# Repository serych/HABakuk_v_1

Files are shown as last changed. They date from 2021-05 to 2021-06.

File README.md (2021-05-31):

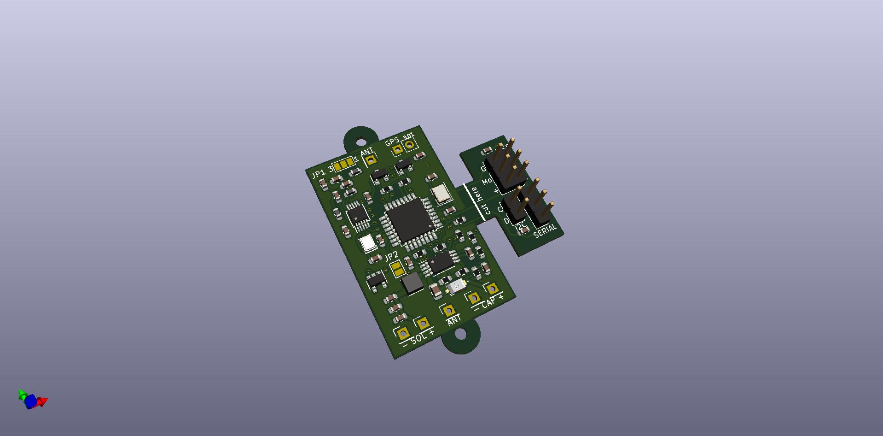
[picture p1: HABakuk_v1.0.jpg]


# HABakuk Pico Balloon Tracker Board

## Introduction:

Design of this board is based on excelent Alain's (K1FM) [K1FM-Pico-Balloon version 1.3](https://github.com/adecarolis).  Why I didn't use Alain's board directly and made my own PCB forked from his design? I was thinking about WSPR balloon tracker design for a long time (approximately 2-3 years) and I wanted simple board with ATmega328, Si5351 and Ublox GPS with possibility to switch peripheries off. From the board designs I found on the Internet, K1FM board met my original ideas the most but:  
- I wanted to power the board by solar panels via MPPT regulator (theorethicaly only two 50 x 25 mm panels would be enought to supply the board)
- I wanted the HF filter, but bypassable to test if the signal penetration is better with or without the filter 
- I'm designing my boards in KiCAD now, so I wanted to redraw the design completely (it is better than trying to import Eagle files) 

## Board construction:
The board includes MPPT power converter based on the SPV1040 chip and the values of the discrete components around it are calculated using [STMicroelectronics eDesignSuite](https://eds.st.com/photovoltaic/) using input parameters Voc = 1200 mV, Imp = 500 mA (measured on two solar panels in series) and Vmp = 930 mV, Imp = 450 mA (my estimation). There is connector for THT electrolytic capacitor serving as the energy store on the board. 

HF filter can be bypassed using **JP1** by scratching off solder jumper contact 1 (which is bridged on PCB by default) and soldering contact 3. 

I'm not sure if the measurement of solar panel voltage by the ATmega will not interfere with the SPV1040 power converter function, so I placed **JP2** on the board (bridged by default) which can be easily scratched off to break the (solar panel -> AD converter input) connection in the case of any problems.
                                                                                                          
The board is designed as 4 layers (only 3 layers used) thin PCB (it has thicknes of 0.8 mm only to reduce the weight of the PCB). Also there is filled zone (GND) only on one side of the board to reduce the weight. All the components except the Ublox GPS module are placed on the top side of the board to make the reflow soldering possible in the amateur conditions.  GPS module on the back side of the board should be soldered as the last component by the soldering iron.      

## Software: 
The recommended softwares are [OrionWSPR](https://github.com/ve3wmb/OrionWspr) or [GeminiWSPR](https://github.com/adecarolis/GeminiWspr)

## Production and real tests
The board will be ordered in [LJCPCB](https://jlcpcb.com/) and I will add here the link to reorder it.

**The board was not yet produced nor tested!** 

Jakub Šerých, serych@panska.cz, [https://jakub.serych.cz](https://jakub.serych.cz) (web only in Czech language)

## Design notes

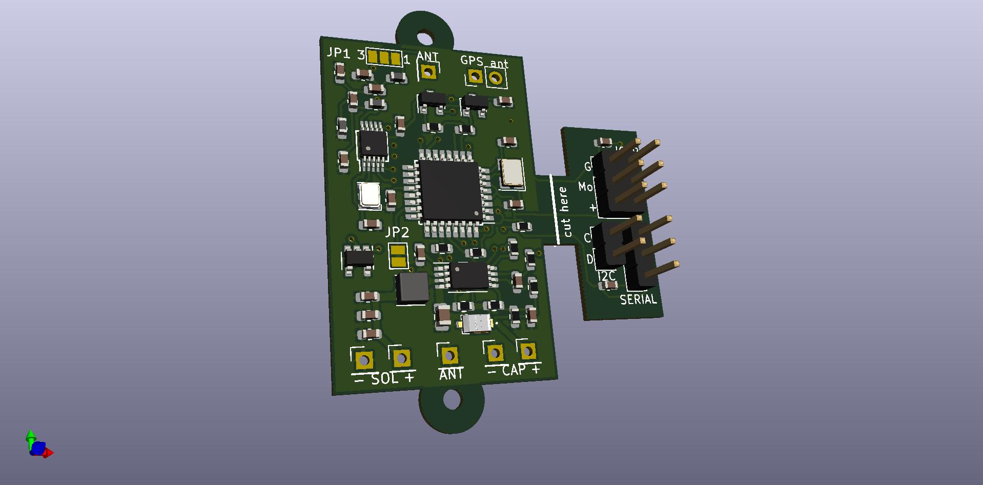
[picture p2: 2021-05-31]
3D views/front.jpg

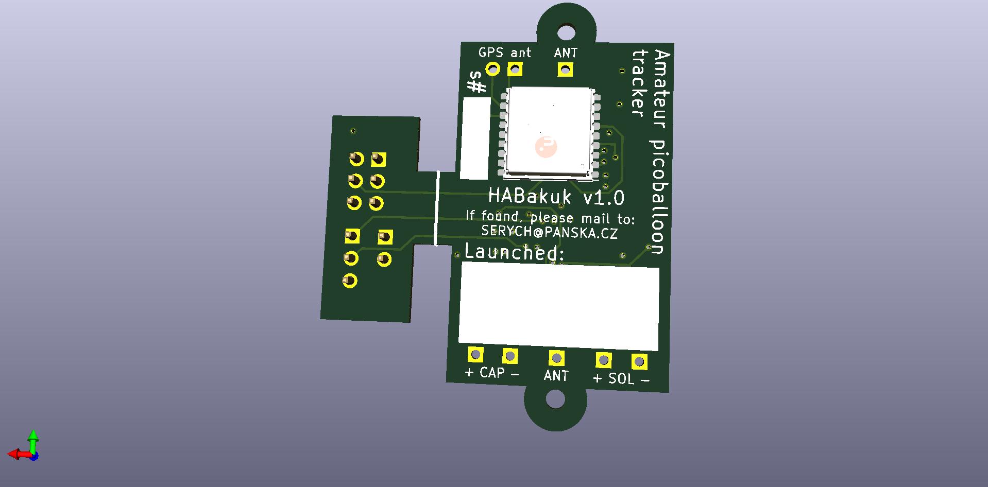
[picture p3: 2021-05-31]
3D views/back.jpg

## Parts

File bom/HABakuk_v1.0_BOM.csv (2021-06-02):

Id | Designator | Package | Quantity | Designation | Supplier and ref
1 | D1 | STMITE | 1 | SMM4F5.0A-TR
2 | J10 | PinHeader_1x01_P2.54mm_Vertical | 1 | C-
3 | J9 | PinHeader_1x01_P2.54mm_Vertical | 1 | C+
4 | J8 | PinHeader_1x01_P2.54mm_Vertical | 1 | SOL-
5 | J7 | PinHeader_1x01_P2.54mm_Vertical | 1 | SOL+
6 | J6 | PinHeader_1x01_P2.54mm_Vertical | 1 | ANT_DWN
7 | J5 | PinHeader_1x01_P2.54mm_Vertical | 1 | ANT_UP
8 | J4 | PinHeader_1x02_P2.54mm_Vertical | 1 | GPS_Ant
9 | J3 | PinHeader_1x03_P2.54mm_Vertical | 1 | SERIAL
10 | J2 | PinHeader_1x02_P2.54mm_Vertical | 1 | I2C
11 | JP2 | SolderJumper-2_P1.3mm_Bridged_Pad1.0x1.5mm | 1 | SolderJumper_2_Bridged
12 | REF**,REF** | MountingHole_2.1mm | 2 | MountingHole_2.1mm
13 | Y1 | Crystal_SMD_Abracon_ABM8G-4Pin_3.2x2.5mm | 1 | Crystal_GND24_Small
14 | U6 | SOT-23-5 | 1 | TMP36GRT
15 | U5 | Oscillator_SMD_Kyocera_2520-6Pin_2.5x2.0mm | 1 | 25MHz
16 | U4 | ublox_MAX | 1 | MAX-M8Q
17 | U3 | MSOP-10_3x3mm_P0.5mm | 1 | Si5351A-B-GT
18 | U2 | TQFP-32_7x7mm_P0.8mm | 1 | ATmega328P-AU
19 | U1 | TSSOP-8_4.4x3mm_P0.65mm | 1 | SPV1040T
20 | R11,R7,R3,R2,R1 | R_0603_1608Metric | 5 | 1k
21 | R10,R9 | R_0603_1608Metric | 2 | 4k7
22 | R8 | R_0603_1608Metric | 1 | 10k
23 | R6 | R_0603_1608Metric | 1 | 220k
24 | R5 | R_0603_1608Metric | 1 | 360k
25 | R4 | R_0603_1608Metric | 1 | 510m
26 | Q2,Q1 | SOT-23 | 2 | SSM3J135TU
27 | L4,L3,L2 | L_0603_1608Metric | 3 | 1,5u
28 | L1 | L_Taiyo-Yuden_MD-3030 | 1 | 10u
29 | JP1 | SolderJumper-3_P1.3mm_Bridged12_Pad1.0x1.5mm_NumberLabels | 1 | fltr
30 | J1 | PinHeader_2x03_P2.54mm_Vertical | 1 | ICSP
31 | C21,C5 | C_0603_1608Metric | 2 | 1u
32 | C20,C16 | C_0603_1608Metric | 2 | 56p
33 | C19,C17 | C_0603_1608Metric | 2 | 18p
34 | C18 | C_0603_1608Metric | 1 | 47p
35 | C15,C10,C8 | C_0603_1608Metric | 3 | 0,1u
36 | C14,C9 | C_0603_1608Metric | 2 | 0,47u
37 | C12,C11 | C_0603_1608Metric | 2 | 15p
38 | C7 | C_0805_2012Metric | 1 | 10u/10
39 | C6,C4 | C_0603_1608Metric | 2 | 1n
40 | C3,C2,C1 | C_0603_1608Metric | 3 | 10u/4

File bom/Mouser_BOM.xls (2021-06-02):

NÁKUPNÍ VOZÍK
Toto není faktura
02-čvn-21 16:34:00
 | Č. Mouser | Výr. Č. | Výrobce | číslo zákazníka | Popis | RoHS: | Životní cyklus | Objednaný počet | Cena (CZK) | Ext.: (CZK)
1 | 377-MAX-8Q-0 | MAX-8Q-0 | u-blox | 16 | Moduly GPS u-blox 8 GNSS LCC module, TCXO, ROM: Due to supply constraint, recommend PN - MAX-8C-0 |  | Mouser nově nabízí | 1 | 488,11 Kč | 488,11 Kč
2 | 511-SPV1040T | SPV1040T | STMicroelectronics | 19 | Řízení baterie Hi efficiency solar battery charger | V souladu RoHS |  | 1 | 74,41 Kč | 74,41 Kč
3 | 511-SMM4F5.0A-TR | SMM4F5.0A-TR | STMicroelectronics | 1 | Ochrana před elektrostatickými výboji / Diody pro potlačení napětí z přechodových jevů 400W HI JCT TMP | V souladu RoHS |  | 1 | 13,10 Kč | 13,10 Kč
4 | 81-GRM188C80G106KE7D | GRM188C80G106KE47D | Murata | 40 | Vícevrstvé keramické kondenzátory MLCC – pro povrchovou montáž SMD, SMT 0603 10uF 4volts *Derate Voltage/Temp | V souladu RoHS |  | 3 | 4,43 Kč | 13,29 Kč
5 | 963-LMK212BJ106KD-T | LMK212BJ106KD-T | Taiyo Yuden | 38 | Vícevrstvé keramické kondenzátory MLCC – pro povrchovou montáž SMD, SMT 0805 10VDC 10uF 10% X5R | V souladu RoHS |  | 1 | 6,45 Kč | 6,45 Kč
6 | 673-PA4334103NLT | PA4334.103NLT | Pulse | 28 | Pevné cívky IND, PWR, 3X3X1.2 10 uH, SMT | V souladu RoHS |  | 1 | 9,54 Kč | 9,54 Kč
7 | 647-UMA0G471MDD | UMA0G471MDD | Nichicon | 50 | Hliníkové elektrolytické kondenzátory – s radiálním vývodem 4volts 470uF 8x5 20% 2.5LS | V souladu RoHS |  | 1 | 9,54 Kč | 9,54 Kč
8 | 652-CRL0603FWR510ELF | CRL0603-FW-R510ELF | Bourns | 25 | Rezistory ke snímání proudu - SMD 0.51ohm 1% 1/10watt | V souladu se směrnicí RoHS na základě výjimky |  | 1 | 4,43 Kč | 4,43 Kč
9 | 667-ERJ-3RED3603V | ERJ-3RED3603V | Panasonic | 24 | Tlustovrstvé rezistory – SMD 0603 Resistor 0.5% 100ppm 360KOhm |  |  | 1 | 2,44 Kč | 2,44 Kč
10 | 71-RCS0603220KFKEA | RCS0603220KFKEA | Vishay | 23 | Tlustovrstvé rezistory – SMD 0.25watt 220Kohms 1% 100ppm | V souladu se směrnicí RoHS na základě výjimky |  | 1 | 3,56 Kč | 3,56 Kč
11 | 755-SDR03EZPF1001 | SDR03EZPF1001 | ROHM Semiconductor | 20 | Tlustovrstvé rezistory – SMD 0603 1Kohm 1% Anti Surge AEC-Q200 | V souladu RoHS |  | 5 | 3,12 Kč | 15,60 Kč
12 | 187-CL03B102KO3NNNC | CL03B102KO3NNNC | Samsung Electro-Mechanics | 39 | Vícevrstvé keramické kondenzátory MLCC – pro povrchovou montáž SMD, SMT 1nF+/-10% 16V X7R 0603 | V souladu RoHS | Mouser nově nabízí | 2 | 2,88 Kč | 5,76 Kč
13 | 187-CL03A105KQ3CSNH | CL03A105KQ3CSNH | Samsung Electro-Mechanics | 31 | Vícevrstvé keramické kondenzátory MLCC – pro povrchovou montáž SMD, SMT 1uF+/-10% 6.3V X5R 0603 | V souladu RoHS | Mouser nově nabízí | 2 | 3,77 Kč | 7,54 Kč
14 | 757-SSM3J135TULF | SSM3J135TU,LF | Toshiba | 26 | MOSFET Small Signal MOSFET P-ch VDSS=-20V, VGSS=+/-8V, ID=-3.0A, RDS(ON)=0.103Ohm @ 4.5V, in UFM package | V souladu RoHS | Nový produkt | 2 | 8,44 Kč | 16,88 Kč
15 | 732-TG252S25MCGNNM3 | TG2520SMN 25.000M-MCGNNM3 | Epson | 15 | TCXO oscilátory TG2520SMN 25.000M-MCGNNM3: TCXO 2.8V 3.3V +/-0.5PPM -40 85C NON O/E250TR | V souladu RoHS | Nový produkt | 1 | 39,56 Kč | 39,56 Kč
16 | 634-SI5351A-B-GTR | SI5351A-B-GTR | Silicon Laboratories | 17 | Generátory hodin a podpůrné produkty I2C Prog, Any Frequency, Any Output, Xtal Ref, 3-Output LVCMOS Clock Gen | V souladu RoHS |  | 1 | 21,54 Kč | 21,54 Kč
17 | 584-TMP36GRTZ-R7 | TMP36GRTZ-REEL7 | Analog Devices Inc. | 14 | Snímače teploty montované na desku -3V TEMPERATURE SENSOR | V souladu RoHS |  | 1 | 42,71 Kč | 42,71 Kč
18 | 810-MLZ1608A1R5WT000 | MLZ1608A1R5WT000 | TDK | 27 | Pevné cívky 0603 1.5uH 20% Large Current | V souladu RoHS | Mouser nově nabízí | 3 | 3,33 Kč | 9,99 Kč
19 | 755-SDR03EZPJ472 | SDR03EZPJ472 | ROHM Semiconductor | 21 | Tlustovrstvé rezistory – SMD 0603 4.7Kohm 5% Anti Surge AEC-Q200 | V souladu RoHS |  | 2 | 2,23 Kč | 4,46 Kč
20 | 80-C0603C150K5RACTU | C0603C150K5RAC7867 | KEMET | 37 | Vícevrstvé keramické kondenzátory MLCC – pro povrchovou montáž SMD, SMT 50V 15pF X7R 0603 10% | V souladu RoHS |  | 2 | 5,32 Kč | 10,64 Kč
21 | 80-C0603C180K5RACTU | C0603C180K5RACTU | KEMET | 33 | Vícevrstvé keramické kondenzátory MLCC – pro povrchovou montáž SMD, SMT 50V 18pF X7R 0603 10% | V souladu RoHS |  | 2 | 5,32 Kč | 10,64 Kč
22 | 581-0603YC470KAT2A | 0603YC470KAT2A | AVX | 34 | Vícevrstvé keramické kondenzátory MLCC – pro povrchovou montáž SMD, SMT 16V 47pF X7R 0603 10% | V souladu RoHS | Nový produkt | 1 | 5,32 Kč | 5,32 Kč
23 | 77-VJ0603D560JXCAJ | VJ0603D560JXCAJ | Vishay | 32 | Vícevrstvé keramické kondenzátory MLCC – pro povrchovou montáž SMD, SMT 0603 56pF 200V C0G 5% HI FREQ | V souladu RoHS |  | 2 | 5,32 Kč | 10,64 Kč
24 | 80-C0603C104K3NAUTO | C0603C104K3NACAUTO | KEMET | 35 | Vícevrstvé keramické kondenzátory MLCC – pro povrchovou montáž SMD, SMT 25V 0.1uF X8L 0603 10% AEC-Q200 | V souladu RoHS |  | 3 | 3,77 Kč | 11,31 Kč
25 | 187-CL10A474KA8NNNC | CL10A474KA8NNNC | Samsung Electro-Mechanics | 36 | Vícevrstvé keramické kondenzátory MLCC – pro povrchovou montáž SMD, SMT 470nF+/-10% 25V X5R 1608 | V souladu RoHS | Mouser nově nabízí | 2 | 2,44 Kč | 4,88 Kč
26 | 71-CRCW060310K0JNEBC | CRCW060310K0JNEBC | Vishay | 22 | Tlustovrstvé rezistory – SMD 1/10Watt 10Kohms 5% Commercial Use | V souladu se směrnicí RoHS na základě výjimky |  | 1 | 2,23 Kč | 2,23 Kč
27 | 710-830055663 | 830055663 | Wurth Elektronik | 13 | Krystaly WE-XTAL 8.0MHz 30ppm 5.0 x 3.2mm | V souladu RoHS | Nový produkt | 1 | 16,87 Kč | 16,87 Kč
Předložením objednávky souhlasítes těmito lhuty a podmínky. (https://cz.mouser.com/saleterms) |  |  |  |  |  |  |  |  | Zboží: | 861,44 Kč
Ceny platí k uvedenému datu a času. |  |  |  |  |  |  |  |  | Přepravné: | 500,00 Kč
 |  |  |  |  |  |  |  |  | Odesílání položek, které nebyly na skladě: | 0,00 Kč

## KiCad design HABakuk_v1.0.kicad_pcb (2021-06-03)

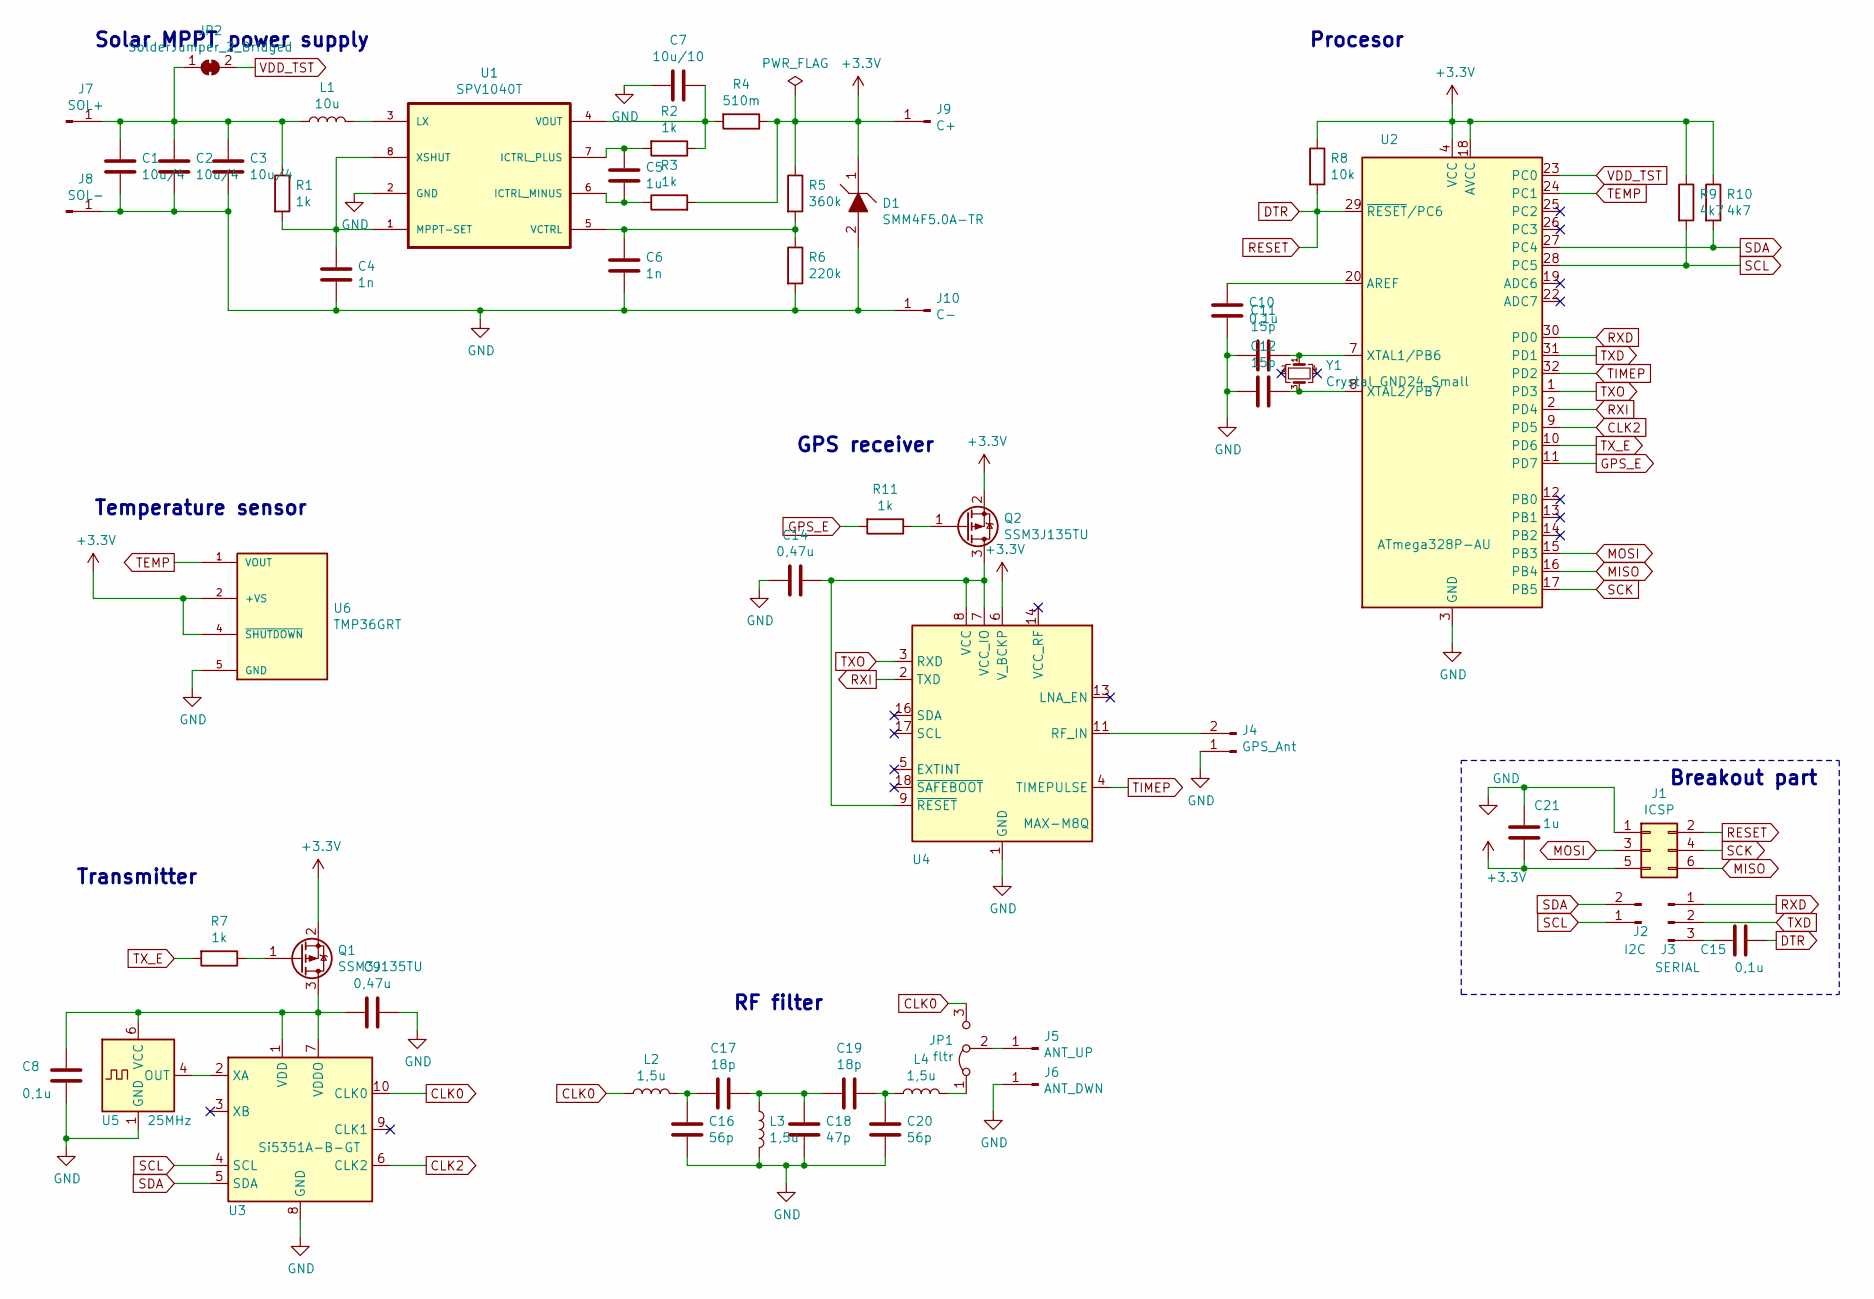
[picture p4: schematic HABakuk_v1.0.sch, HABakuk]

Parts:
C1, C2, C3: 10u/4; C_0603_1608Metric
C4, C6: 1n; C_0603_1608Metric
C5, C21: 1u; C_0603_1608Metric
C7: 10u/10; C_0805_2012Metric
C8, C10, C15: 0,1u; C_0603_1608Metric
C9, C14: 0,47u; C_0603_1608Metric
C11, C12: 15p; C_0603_1608Metric
C16, C20: 56p; C_0603_1608Metric
C17, C19: 18p; C_0603_1608Metric
C18: 47p; C_0603_1608Metric
D1: SMM4F5.0A-TR; STMITE; Mouser Part Number 511-SMM4F5.0A-TR
J1: ICSP; PinHeader_2x03_P2.54mm_Vertical
J2: I2C; PinHeader_1x02_P2.54mm_Vertical
J3: SERIAL; PinHeader_1x03_P2.54mm_Vertical
J4: GPS_Ant; PinHeader_1x02_P2.54mm_Vertical
J5: ANT_UP; PinHeader_1x01_P2.54mm_Vertical
J6: ANT_DWN; PinHeader_1x01_P2.54mm_Vertical
J7: SOL+; PinHeader_1x01_P2.54mm_Vertical
J8: SOL-; PinHeader_1x01_P2.54mm_Vertical
J9: C+; PinHeader_1x01_P2.54mm_Vertical
J10: C-; PinHeader_1x01_P2.54mm_Vertical
JP1: fltr; SolderJumper-3_P1.3mm_Bridged12_Pad1.0x1.5mm_NumberLabels
JP2: SolderJumper_2_Bridged; SolderJumper-2_P1.3mm_Bridged_Pad1.0x1.5mm
L1: 10u; L_Taiyo-Yuden_MD-3030
L2, L3, L4: 1,5u; L_0603_1608Metric
Q1, Q2: SSM3J135TU; SOT-23
R1, R2, R3, R7, R11: 1k; R_0603_1608Metric
R4: 510m; R_0603_1608Metric
R5: 360k; R_0603_1608Metric
R6: 220k; R_0603_1608Metric
R8: 10k; R_0603_1608Metric
R9, R10: 4k7; R_0603_1608Metric
U1: SPV1040T; TSSOP-8_4.4x3mm_P0.65mm
U2: ATmega328P-AU; TQFP-32_7x7mm_P0.8mm
U3: Si5351A-B-GT; MSOP-10_3x3mm_P0.5mm
U4: MAX-M8Q; ublox_MAX
U5: 25MHz; Oscillator_SMD_Kyocera_2520-6Pin_2.5x2.0mm
U6: TMP36GRT; SOT-23-5; PARTREV H
Y1: Crystal_GND24_Small; Crystal_SMD_5032-4Pin_5.0x3.2mm

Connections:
+3V3: C21.2, D1.1, J1.5, J9.1, Q1.2 (S), Q2.2 (S), R3.2, R4.1, R5.1, R8.1, R9.1, R10.1, U2.4 (VCC), U2.6 (VCC), U2.18 (AVCC), U4.6 (V_BCKP), U6.2 (+VS), U6.4 (~SHUTDOWN)
CLK0: JP1.3 (B), L2.1, U3.10 (CLK0)
CLK2: U2.9 (PD5), U3.6 (CLK2)
DTR: C15.1, J1.2, R8.2, U2.29 (~RESET~/PC6)
GND: C1.2, C2.2, C3.2, C4.2, C6.2, C7.2, C8.2, C9.1, C10.2, C11.2, C12.2, C14.2, C16.2, C18.2, C20.2, C21.1, D1.2, J1.1, J4.1, J6.1, J8.1, J10.1, L3.2, R6.2, U1.2 (GND), U2.3 (GND), U2.5 (GND), U2.21 (GND), U3.8 (GND), U4.1 (GND), U4.10 (GND), U4.12 (GND), U5.1 (GND), U5.3 (GND), U6.5 (GND)
GPS_E: R11.2, U2.11 (PD7)
MISO: J1.6, U2.16 (PB4)
MOSI: J1.3, U2.15 (PB3)
unnamed: C1.1, C2.1, C3.1, J7.1, JP2.1 (A), L1.1, R1.1
unnamed: C4.1, R1.2, U1.1 (MPPT-SET), U1.8 (XSHUT)
unnamed: C5.1, R2.2, U1.7 (ICTRL_PLUS)
unnamed: C5.2, R3.1, U1.6 (ICTRL_MINUS)
unnamed: C6.1, R5.2, R6.1, U1.5 (VCTRL)
unnamed: C7.1, R2.1, R4.2, U1.4 (VOUT)
unnamed: C8.1, C9.2, Q1.3 (D), U3.1 (VDD), U3.7 (VDDO), U5.6 (VCC)
unnamed: C10.1, U2.20 (AREF)
unnamed: C11.1, U2.7 (XTAL1/PB6), Y1.1
unnamed: C12.1, U2.8 (XTAL2/PB7), Y1.3
unnamed: C14.1, Q2.3 (D), U4.7 (VCC_IO), U4.8 (VCC), U4.9 (~RESET)
unnamed: C15.2, J3.3
unnamed: C16.1, C17.2, L2.2
unnamed: C17.1, C18.1, C19.2, L3.1
unnamed: C19.1, C20.1, L4.1
unnamed: J4.2, U4.11 (RF_IN)
unnamed: J5.1, JP1.2 (C)
unnamed: JP1.1 (A), L4.2
unnamed: L1.2, U1.3 (LX)
unnamed: Q1.1 (G), R7.1
unnamed: Q2.1 (G), R11.1
unnamed: U3.2 (XA), U5.4 (OUT)
RXD: J3.1, U2.30 (PD0)
RXI: U2.2 (PD4), U4.2 (TXD)
SCK: J1.4, U2.17 (PB5)
SCL: J2.1, R9.2, U2.28 (PC5), U3.4 (SCL)
SDA: J2.2, R10.2, U2.27 (PC4), U3.5 (SDA)
TEMP: U2.24 (PC1), U6.1 (VOUT)
TIMEP: U2.32 (PD2), U4.4 (TIMEPULSE)
TXD: J3.2, U2.31 (PD1)
TXO: U2.1 (PD3), U4.3 (RXD)
TX_E: R7.2, U2.10 (PD6)
VDD_TST: JP2.2 (B), U2.23 (PC0)

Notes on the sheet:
Breakout part
Transmitter
RF filter
Temperature sensor
GPS receiver
Solar MPPT power supply
Procesor

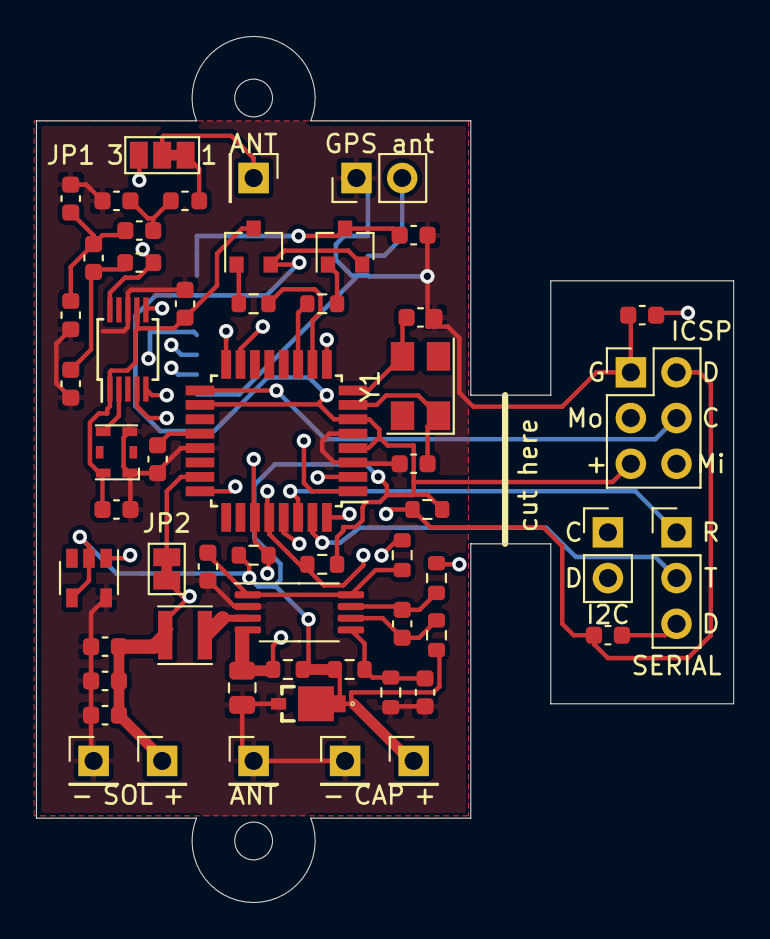
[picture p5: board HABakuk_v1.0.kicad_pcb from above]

Board: 4 copper layers, 38.7 x 48.1 mm, 57 parts (1 on the bottom side), 41 nets.

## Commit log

2021-06-02 Added BOMs, modified 8 MHz crystal footprint
    [HABakuk_v1.0.kicad_pcb, HABakuk_v1.0.sch]
2021-06-02 Added BOMs
    [HABakuk_v1.0_BOM.csv, HABakuk_v1.0_BOM.xlsx, Mouser_BOM.xls]
2021-06-03 Fabrication files added
    [HABakuk_v1.0-B_Cu.gbl, HABakuk_v1.0-B_Cu.gbr, HABakuk_v1.0-B_Mask.gbr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]
